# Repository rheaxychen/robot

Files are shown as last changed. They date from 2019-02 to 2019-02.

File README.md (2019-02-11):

# Stair Climbing Robot

*Team 9 - ENGR 202 - Winter 2018 - University of Washington*

Final deliverable can be viewed here: [project deliverable](./stair-climbing-robot-deliverable.pdf), [presentation poster](./Poster/poster.pdf). 

### Reference for file names

*CAPITAL CHARACTER*

- 0 - Cover Profiles Contracts
- A - Project Selection
- B - Project Proposal
- C - Design Concept
- D - Preliminary Design

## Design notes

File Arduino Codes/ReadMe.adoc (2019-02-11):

:Author: aaronsu
:Email: aaronsu@uw.edu
:Date: 02/02/2018
:Revision: version#
:License: Public Domain

= Project: {Project}

Describe your project

== Step 1: Installation
Please describe the steps to install this project.

For example:

1. Open this file
2. Edit as you like
3. Release to the World!

== Step 2: Assemble the circuit

Assemble the circuit following the diagram layout.png attached to the sketch

== Step 3: Load the code

Upload the code contained in this sketch on to your board

=== Folder structure

....
 sketch123                => Arduino sketch folder
  ├── sketch123.ino       => main Arduino file
  ├── schematics.png      => (optional) an image of the required schematics
  ├── layout.png          => (optional) an image of the layout
  └── ReadMe.adoc         => this file
....

=== License
This project is released under a {License} License.

=== Contributing
To contribute to this project please contact aaronsu <aaronsu@uw.edu>

=== BOM
Add the bill of the materials you need for this project.

|===
| ID | Part name      | Part number | Quantity
| R1 | 10k Resistor   | 1234-abcd   | 10       
| L1 | Red LED        | 2345-asdf   | 5        
| A1 | Arduino Zero   | ABX00066    | 1        
|===

=== Help
This document is written in the _AsciiDoc_ format, a markup language to describe documents. 
If you need help you can search the http://www.methods.co.nz/asciidoc[AsciiDoc homepage]
or consult the http://powerman.name/doc/asciidoc[AsciiDoc cheatsheet]

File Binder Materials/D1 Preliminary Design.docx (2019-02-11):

Aaron Su

Caelen Coe

Noah Whelan

Mahamed Dirie

Rhea Chen

Valentina Valero

# Preliminary Design

### Electrical System Schematic

<Insert at end of lab>

Technical Drawing

No major changes have been made since the previous Technical Drawing Section. Please refer to Concept Design section “Preliminary Technical Drawings” and figures 5-10 for all technical drawings.

### Digital Models

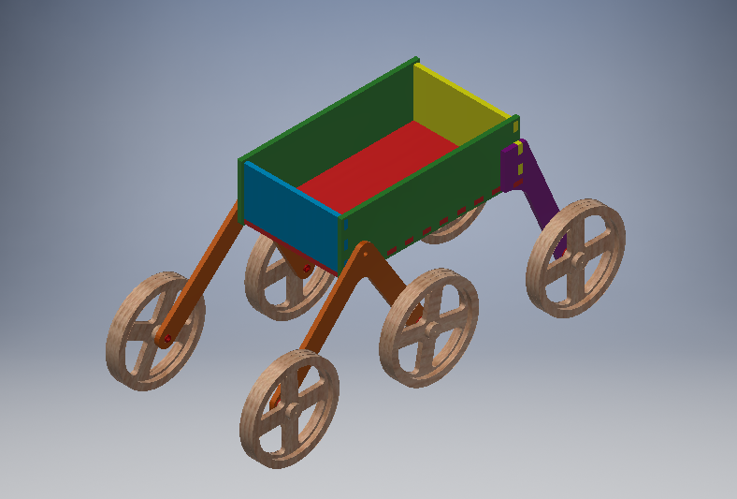
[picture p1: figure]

Figure 2: Design 1, Isometric View of Parts

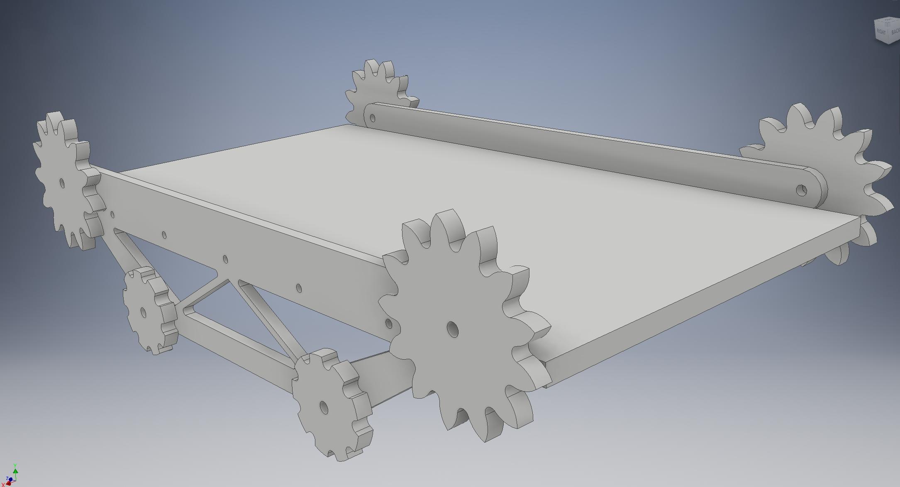
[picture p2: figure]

Figure 2: Design 2, Isometric View of Parts

Both designs are assembled and can be seen in Figure 1 for Design 1 and Figure 2 for Design 2. Design 1 and Design 2 will both take advantage of laser cutting when possible in order to save time and PLA material. This means the panels of the chassis, wheels (Design 1), supports for drive train (Design 1 and 2) and sprockets (Design 2) will all be laser cut. Smaller pieces, such as the axles in Design 1 and individual tracks on Design 2 will be 3D printed in order to be accurate and be made out of non-wood material.

Both designs use a simple chassis that is a rectangular box in order to conveniently have access to the electronic systems of the robot. In addition, the rectangular box is hollow in order to reduce weight, and leave room for the 1.5 kilogram weight that will be carried on board. The drive train will attach to the chassis in order to ensure the robot can be held together.

Design 1 takes advantage of wheels in order for the weight to be light and the frame to be rotatable in order to climb stairs. The front wheels are attached in order to maximize surface area contact with the stairs. Each wheel is also independently powered in order to allow “full-wheel drive” and generate torque when the wheels are in contact with any surface. The back wheel does not rotate since having all sets of wheels rotatable will make the robot unstable when climbing over multiple stairs. The back wheel is meant as an extra surface to ensure the robot will not fall backwards. This design will require an additional H-bridge, axles, and two motors in comparison to Design 2.

The files for Design one are specifically as follows:

Axel and Wheels

- Axel.ipt
- Front Wheel Base.ipt
- Rear Wheel Base.ipt
- Wheel Inner Ring.ipt
- Wheel Inner Spacer.ipt
- Wheel Main.ipt
- Wheel Outer Right.ipt

Vehicle Panels

- Vehicle Bottom Panel.ipt
- Vehicle Front Panel.ipt
- Vehicle Rear Panel.ipt
- Vehicle Side Panel.ipt

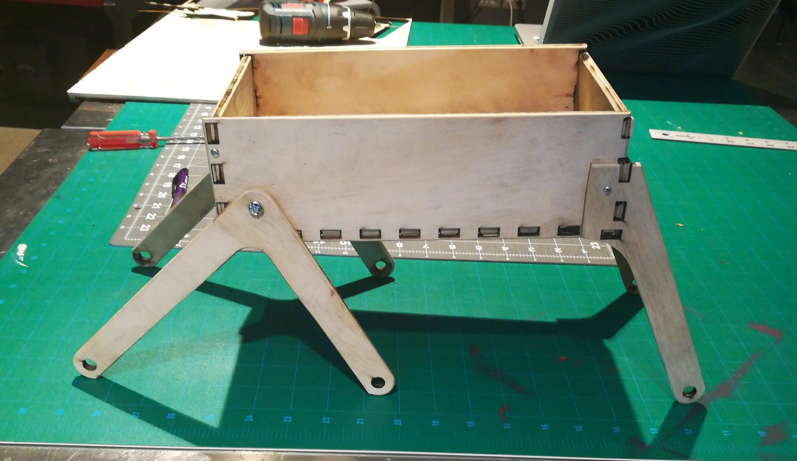
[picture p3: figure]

Figure 3: Design 1, Prototype Side View

In addition, a prototype cutout was made for Design 1 (Figure 3). This was cut out of birch wood to show that the design was technically feasible.

Design 2 is still in development, but Figure 2 shows a mostly completed CAD assembly. Design 2 mainly differs from Design 1 in that it will require more than 6 feet of track as opposed to 6 wheels. The track will be powered by 4 motors (2 on each side) in order to supply enough torque. The traction problem is also solved by having a continuous surface in contact with the stairs, albeit in a less flexible shape than Design 1. The gear design will also provide greater torque to the robot’s drivetrain since the speed will be reduced. Design 2 will require fewer electronics components (as stated above) but will require more material and potentially stronger motors in order to work.

### Simple Machines

Design 1 features a lever for the front 4 wheels and a wheel and axle for each of its 6 wheels. The second class lever will get its force from when the wheels apply a force to the stairs and the stairs push back. This will cause the level to rotate around the fulcrum, which is on the robot chassis, and allow the wheels to climb up the stairs and bring the robot with it. This is a simple machine since the force from the stairs pushing back moves the robot, causing work to be done. The wheel and axle machines found on each of the 6 wheels allow a motor to spin each wheel and axle at the same rate in order to cause the robot to drive. The wheel and axle are simple machines on this robot since they apply a force (from the motors) to move the robot and spin themselves. In combination with the lever on the front wheels, the robot will be able to climb stairs since the wheels can move the whole robot and the level will allow the robot to rotate in order to climb stairs.

Design 2 features gears that are used to power the tracks. The tracks will lay into the gears (of two different ratios) in order to supply maximum torque when the robot is climbing up the stairs. Torque is important in order to overcome gravity and climb up the stairs, meaning the gears are designed to be slow but powerful. It is a simple machine because it helps the robot apply a force coming from the motors against the ground in order to do work to get up the stairs.

The main reason there are two designs is so that we can test the functionality of these two simple machines. Design 1 uses more machines in order to increase the surface area and power applied to the surface through its lever and wheels. Design 2 uses gears to provide torque to the track, but has a smaller surface area by being unable to rotate. As both designs are tested, there will be much emphasis placed on how the design of the simple machines will affect the robot performance.

### Updated Bill of Materials

No major changes have been made since the previous Updated Bill of Materials Section. Please refer to Concept Design section “Updated Bill of Materials” and “Table 1: Updated Bill of Materials Table”.

ENGR202 – Winter 2018 Team 9

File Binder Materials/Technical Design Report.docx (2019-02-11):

Technical Design Report

The Technical Design Report is your chance to show off your project. Explain what you have done this quarter and why it’s impressive. A working project is more important than a well written report, keep your writing brief and to the point.

Your Technical Design Report should at least include the following:

  Explain the changes your design has gone through since the Preliminary Project
  Design and why you made those changes:

Since the preliminary project design the stair climbing robot has changed significantly. The design that incorporated two independent pairs of rhomboid tank treads was reconsidered due to time and material restraints. Ultimately, the group decided that this design would most likely be too costly and complicated. From there the mechanical team split into two different groups. One of these groups designed a robot that utilized a single pair of large trapezoidal tank treads, with two motors powering each tread. The second team designed a robot that utilized six independently powered and controlled wheels attached to stilts that separate them from the chassis. Two pairs of wheels would be connected together at the front of the robot and would be attached to the chassis via an axle that allowed the wheels to rotate around the surface of the stairs. The rear pair of wheels were rigidly attached to the chassis. When each design had been completed we analyzed them as a team to determine which to pursue. Though it was difficult to tell which would perform better at climbing stairs, our team decided that the production of treads for the tank design would be prohibitively time consuming compared to the wheeled design. In addition, the tracked design would require more power and more weight than the wheeled design, ultimately deciding the wheeled design would lead to a better outcome.

Having agreed upon the wheeled design it was prototyped and tested it. During the design iterations several important changes were made. Our first prototype did not have sufficient power to climb the stairs. To remedy this we first replaced our initial small 9 volt DC motors with similar but much more powerful ones. These new motors were 12 volts and ran at 30 RPM or 100 RPM. Secondly, the second prototype chassis was constructed out of acrylic, as opposed to the wood in the first design. This was done to save weight and reduce the amount of torque needed to pull the robot up the stairs. In our third design iteration we added braces to the two forward axles to reduce flexing that caused the wheels to lock up. In addition, after several of our axles snapped we designed new stronger axles that were able to withstand the stress of going up stairs. Springs were also attached to the front-most section of the robot to pull up the robot after the front wheels ran into a flight of stairs. These major changes are what have allowed the robot to improve from being unable to even move up a slight ramp to reliably climbing stairs.

  Include new models and technical drawings

Sections of Chassis (Caelen’s files)

New Acryllic cutouts

  Describe the process you went through in building your projects
  Include process pictures if you have them
  Pictures of completed project

Briefly (1 - 2 paragraphs) describe some of the challenges you faced in the design and building process, and how you overcame these challenges.

Some of the primary challenges we faced during the creation of the robot arose due to monetary and time constraints. In the process of designing our robot we considered multiple designs that incorporated a continuous track or tread. The most time efficient way of creating such a robot would have been to purchase a manufactured tread or belt, 3D printed tracks would have taken too long to print and assemble. Unfortunately we could find no belts of appropriate specifications that would left room in our budget for other important components. Had we the time to print all the necessary track or the money to purchase tread we could have more seriously considered using a tracked robot. Other obstacles also increased the challenge that time posed. One example of this was our reliance on the Dabble Lab. Several times throughout our build process equipment failure meant we would lose a day of work time. Conflicting schedules meant we could often only meet a couple times in a week, meaning a delay of just a day could put us more than half a week behind.

Overcoming these challenges meant adapting our design methods and time management. During our initial design phase we had to take a close look at the feasibility of each proposed design. While the tracked design certainly had its benefits over some of the others, ultimately we determined it to be an unrealistic design path. For all it’s pros it was simply to time consuming to pursue. To save resources and time we stopped our prototyping of tracked designs and put all our effort into producing a functioning prototype that used wheels. Doing this allowed us to fast track our primary design while minimizing waste on designs we couldn’t reasonable build. Time management was also vital in keeping our team on track to complete the robot within the set time constraints. We began to anticipate the possibility of equipment failure. When we planned work sessions we would often set a backup time in the event we couldn’t use the required equipment for progress. We also extended the length of our work sessions to make up for time we had lost previously and to negate the effect of future delays. By proactively responding to these obstacles we have been able to complete our robot on time and within budget.

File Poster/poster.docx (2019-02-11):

It must include what is your project and goal(s). What was the design process? use things such as sketches, CAD, pics of the design, schematics and diagrams to show this. What were the results of your project? Conclusion: whether you met your goals, challenges, next steps if your were to continue.

*** Make a folder/powerpoint all all our pictures used in the presentation so that we have them to present as well***aar

Project

Build a robot that can climb a set of stairs

Robot should be autonomous and hold its own power source

Robot should be able to handle stairs of different sizes

Goals

1. Drive on a level surface
2. Drive on a ramp
3. Drive up and down a set of stairs
4. Operate the Robot with Bluetooth

Design Process:

Concept Design - Narrowed down to two

- Pictures: Sketches of both designs

CAD Designs - Initial concepts of both

- Pictures: CAD of both

Build Designs - Caelan and Noah working in lab

- Pictures: Noah/Caelan Working

Build Electronics - Schematics

- Pictures: Valentina’s electrical schematic

Program - Pseudocode then actual

- Pictures: code (at bottom)

Assemble - Put it all together

- Pictures: Wood design

Test

- Pictures: Us testing

Model 2 - Acryllic

- Pictures: of acryllic bot

Test

- Pictures: More test pictures

Final Design

Conclusion

What we achieved

Robot was fully built and functional

All goals stated above

Challenges:

Choosing the right design

Making the robot powerful enough while minimizing the overall weight

Getting enough power to run the whole style

Building alternate set of stairs when our original design wasn’t working

Next Steps:

Make all motors 12 Volt, 100 rpm motors

Switch out batteries to 12 Volts (currently 18 Volts) to avoid damaging Hbridges

Switch wheel material to rubber to get more traction

Add sensors and accelerometers to get more feedback from robot

Get to point it can climb human-sized stairs

Put on poster:

Stronger Motors

Add Sensors

18V -> 12V Batteries

Pictures

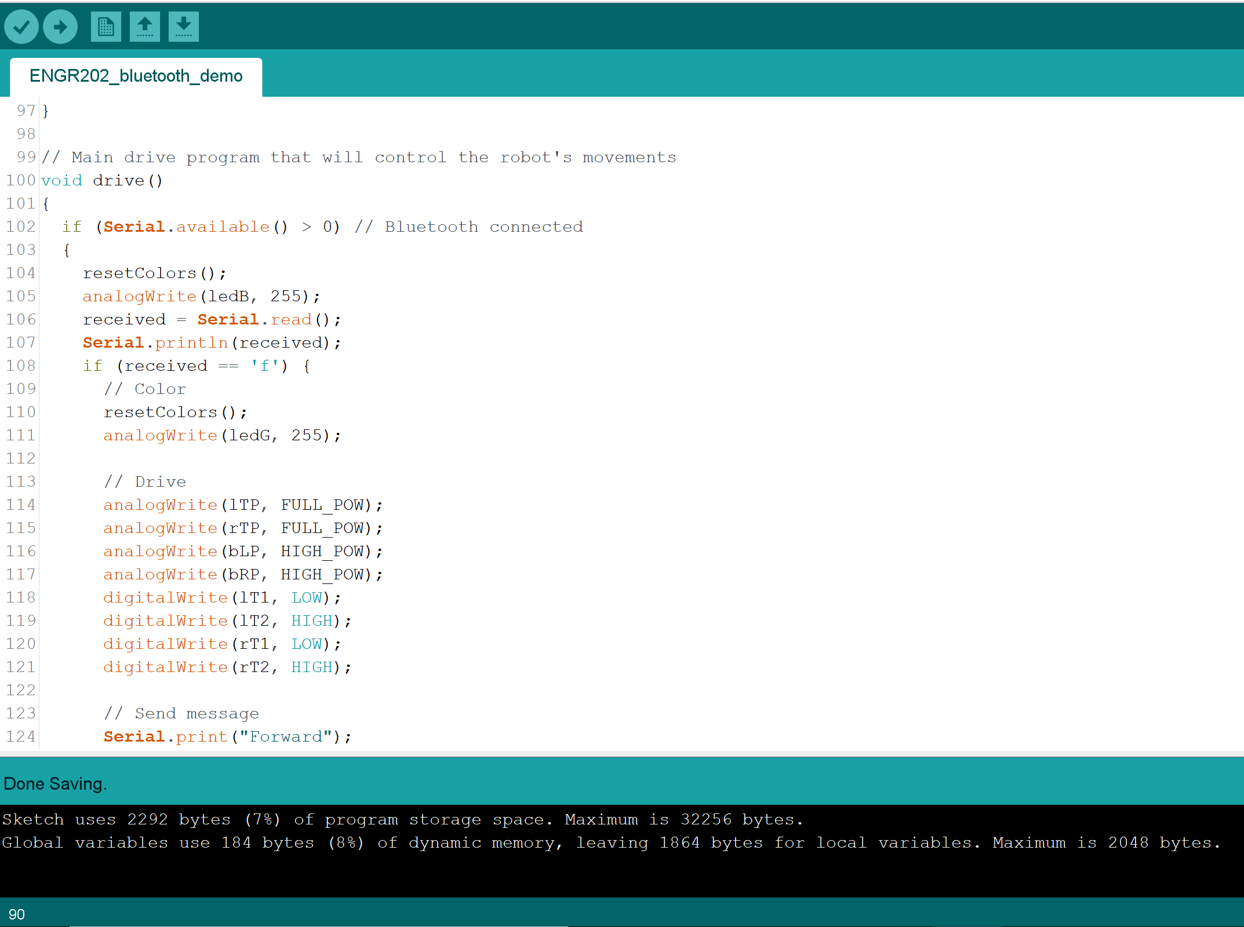
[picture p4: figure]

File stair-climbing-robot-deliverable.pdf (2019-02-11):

1 | P a g e

2 | P a g e

## Table of contents

I. Profiles | 3-6
II. | Team Contract | 7
III. | Project Selection | 8-
| 12
IV. | Project Proposal | 13-21
V. Concept Design | 22-33
VI. | Preliminary Project Design | 34-39
VII. | Technical Design Report | 40-58

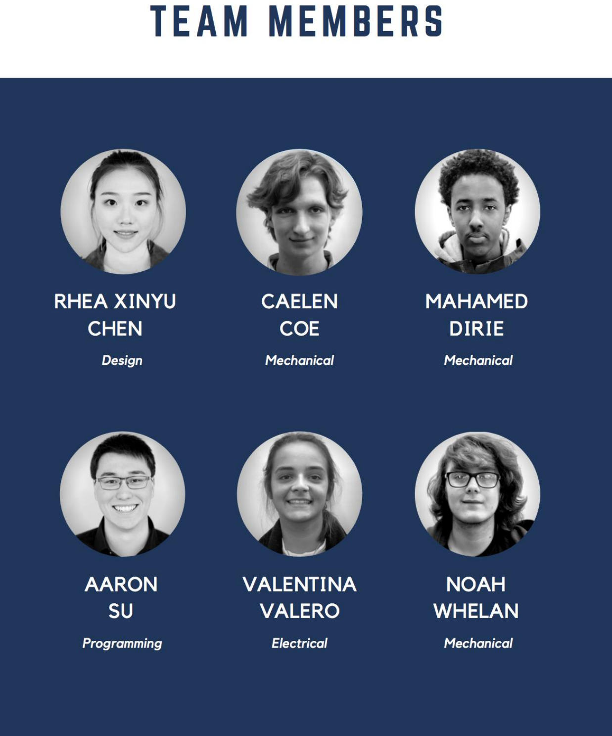
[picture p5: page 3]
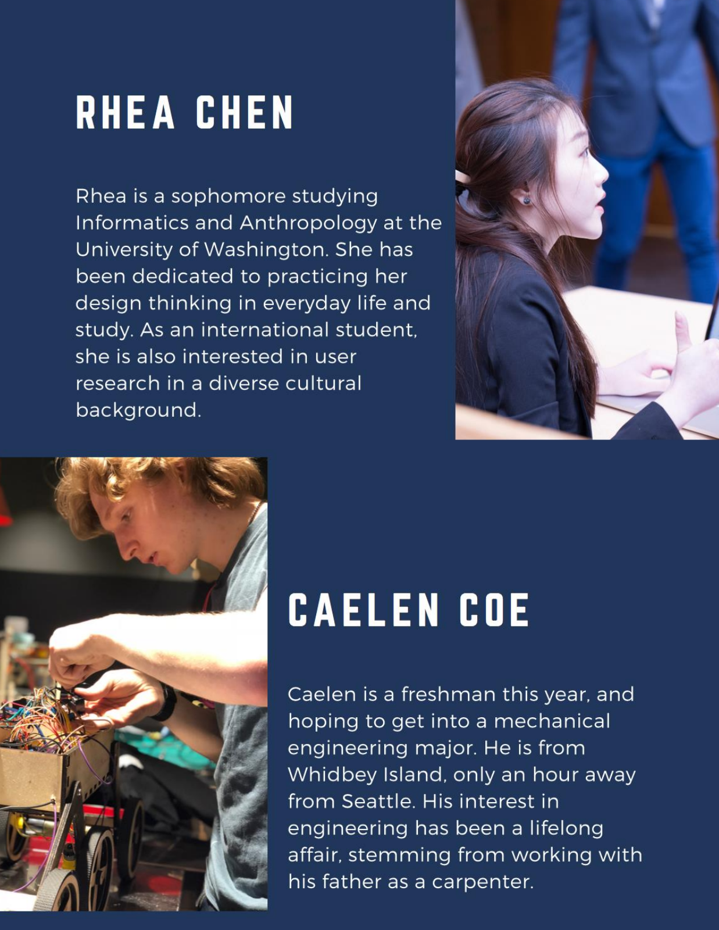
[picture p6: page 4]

4 | P a g e

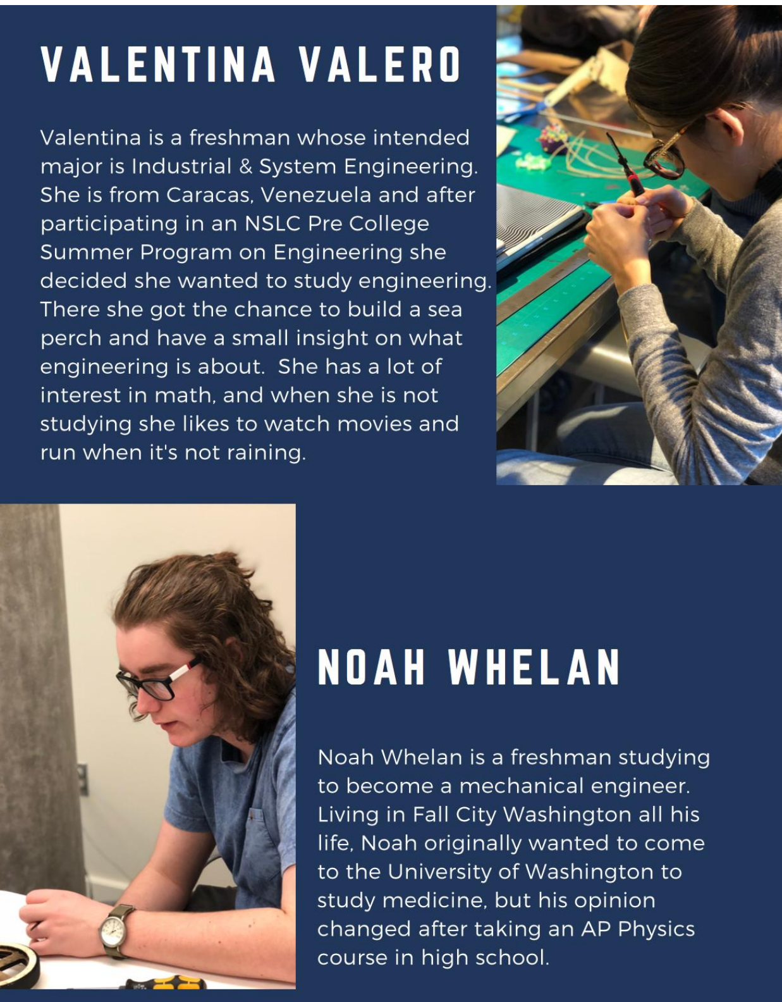
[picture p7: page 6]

6 | P a g e

## Team Contract

## All team members shall do as follow to ensure the best and most successful work environment:

## - Be on time - If you are late, communicate - Be patient - Teach each other - Be responsible - Be honest - Be encouraging - Communicate on Slack - Do not be stubborn when stubbornness is not required - Ask questions if you have any - Solve problems as they arise

8 | P a g e

## Project Selection

Introduction

The members of our team individually brainstormed ideas that the whole team could potentially work on during the quarter. After researching different robots and ideas, each project idea was given a paragraph description under “Project Ideas”. Then, an overall group rating for each project was made in a “Decision Matrix”, allowing the group to narrow down the choices from five to three. These final three selections will be among those considered for the final project, which was selected in the very final section.

Project Ideas

1. Gardening Robot

This project would involve a robot that is able of managing the gardening of a plant. The steps in the planting process which the robot will be capable of are driving in soil, digging up soil, dropping a seed, watering the seed, and fertilizing the seed. This robot has real-world applications that involve simplifying the gardening and farming process that could be used on a personal or industrial level. The parts required for the robot would involve containers and release systems for the seeds, water, and fertilizer that would involve valves and switches. The digging process would involve a motor attached to a drill-like object. FarmBot Genesis is a similar robot on the market that can plant a seed with a seed injector and water it precisely, build regimens for taking care of a plant by using its sensors to detect outside conditions, detect weeds and destroy them too (FarmBot.io, 2016)

2. Object rejection and counting machine (ORCM)

This project would be a robot whose purpose is to reject items that do not fulfill a specific condition, related to size and weight. This would be similar to the “conveyor belt sorting bot” created by Gurmeet Sharma that is able to sort objects based off height (Sharma, 2009). In this example, the object rejection and counting machine has a conveyor belt and a sensor that identifies the size of the object, if the object doesn’t fulfill the condition, it is pushed out of the conveyor belt. It is very useful for quality control and inventory in factories as it can sort out anything that does not satisfy a condition. For example, it can determine whether a tennis ball fulfills certain criteria for size and weight for them to correctly perform. It can also be applied to determine the type of coin based on the weight and size. This project will likely require buying parts because it has a conveyor belt system that uses two or more pulleys; and a load sensor to determine the weight. From the provided parts this project will require a DC motor.

3. Companion Bot

This project would involve an autonomous robot that follows a device through Bluetooth or wireless communication. The robot would be similar to companion bots like Kuri, meant to follow a person around while providing auxiliary services (NBC News, 2017). Kuri is a companion bot that fulfills a wide range of functions that include recognition of faces, playing music or working as an alarm. The robot can respond to the touch and can moves around through any surface thanks to a set of sturdy wheels. Rather than providing all the same functionality as Kuri, the robot would only follow a person around and hold materials that person finds useful (water bottle, phone, speaker, etc.) These personal items will be able to add supportive services to the robot, such as playing music. This project would be useful as a prototype to see how people will want to interact with an autonomous companion bot. The project will focus on avoiding obstacles using distance sensors, following an object through Bluetooth communication, and 3-D printing a customized robot frame to fit the personal items. This project will require a Bluetooth-capable device to communicate with the robot, but a phone with such capabilities is owned by all members of the group.

10 | P a g e
4. Stair Climbing Vehicle

Semi tracked vehicle with ability to climb stairs. Basic design would consist of four independently driven tracked wheels, and an adjustable wheelbase. Would need to have ability for object and environment detection and obstacle avoidance. Required parts would be infrared or some sort of LIDAR for object detection, on-board cameras for driver visuals, multiple motors and servos for movement. An example of the final robot would be like the robot designed by Transcend, which is built to assist police by climbing upstairs using a tread drive base (Transcend Tactical, 2018). Thought the example is much more complex than what is being planned, the robot can ascend 3 steps at a time in up and down articulated movements that produce a downward compression force.

5. Kitchen Aid Robot

This project would be an autonomous robot that could crack an egg by following set movements, or a robot that could make a cookie dough given the specific amount of each ingredients. This robot will only focus on one single task following a pre-programmed set of movements similar to Molly’s Kitchen Robot prototype (UPHIGH, 2016). This bot will be able to use a motor to spin, raise, and lower the arm, and use precise movements to ensure nothing gets broken in the process. The robotic kitchen has a pair of fully articulated hands that reproduce human movements when cooking and is operated through a touch screen. This project will save people time and effort in cooking. To prevent it from crashing due to water, we would add water-proof layer to it.

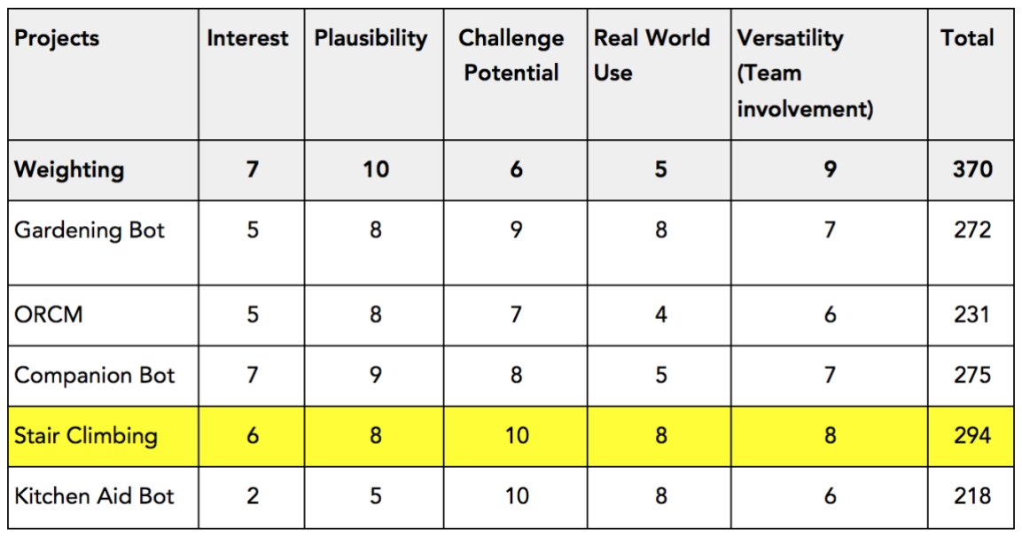
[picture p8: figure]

Decision Matrix

Table 1 - Decision Matrix

In our Decision Matrix (Table1), interest (Col.2) was our third most important category in order to keep us motivated throughout the quarter in order to want to spend time on this project. Plausibility (Col.3) was the most important category to our group since we all wanted a finished product at the end of the quarter with the parts provided. Similarly, versatility (Col.6) was our second most important category since we wanted to keep all interested team members involved in a project they could finish. Challenge potential (Col.4) was also considered so that if a particular part of the project was done quickly, there was the ability to increase the scope of the project. Also, challenge helps us think out of the box to help us solve problems that may come up. Finally, real-world usage (Col.5) was considered since our project is a prototype to solve a real-world issue.

12 | P a g e

1st Choice - Stair Climbing

The team thinks this project would provide a challenge in design and execution, and is thus our top choice. We also believe that the driving mechanics associated with independently powered wheels would be sufficient work for the mechanical, electronic, and programming sub-teams. There is potential in this project to be able to handle different stair sizes ranging from smaller than the robot’s wheels to human-designed stairs, meaning we can adapt this project to our engineering ability.

2nd Choice - Companion Bot

This project allows for a creative component and allowance for differing levels of complexity. The idea of making a robot for personal use is one that appealed to many members of the group, as it would serve our own purposes after it is complete. Also, the challenge of getting a robot to drive and follow a device should give the programming and electronics sub-team plenty to work on.

3rd Choice - Gardening Robot
This project is the most multifaceted of the three final projects since it will do more than just drive. The different subsystems required to fully garden a plant provide plenty of opportunities to design creatively and allow the project to adapt to our own skill sets. The practicality of the bot combined with the team involvement and ability to finish it make this one of our top three choices.

Final Decision

As our final decision, we decided to work on the stair climbing robot due to its challenge potential for both the mechanical and electrical sub-teams. There are many possibilities in the design of the robot as well, which gives our team opportunity to brainstorm.

## Project Proposal

Introduction

Robots are increasingly being integrated into working tasks to replace in many fields of applications such as military, security systems, agriculture and industry. The project’s goal is to prototype a specific implementation of a stair-climbing robot in order to contribute to the body of knowledge and work done in this field of robotics. The robot’s functionality will focus on being able to climb up a set of stairs as well as move over a flat surface, and rather than building the robot with expensive materials or the most advanced machinery, the project will focus on applying fundamental engineering principles and a relatively small budget to design, prototype, and build the robot. This will allow the project to be accessible and by any individual or group that has a basic understanding of engineering design, such as students in an undergraduate introductory engineering course.

Problem Statement

For military/police investigation, surveillance, urban search and rescue missions is often necessary to place sensors and cameras to get better awareness for the rescue personnel on the situation in order to determine how to proceed, for this reason stair climbing robots are a great alternative to reach dangerous or inaccessible areas just by the use of a control remote. Robots have a clear advantage over humans in these situations and the benefits to this operation of rescue robots, such as a stair climbing robot, include reduced personnel requirements, reduced fatigue, and access to unreachable areas. Robots are predestined to complete this task, but the requirements for such mobile systems are demanding. They should be quick and agile and, at the same time, be able to deal with rough terrain and even to climb stairs. By finding effective ways for robots to climb stairs, the safety of professions including firefighting, relief workers, soldiers, police officers, security guards, and professional movers will increase.

14 | P a g e

Objectives

1. Moving on a Flat Surface

The robot should be able to move on a level ground at a constant speed of 0.894 mps. We decided the speed taking as a reference the walking speed. Constant speed is important for comfortable driving over surfaces that aren’t stairs, which many stair-climbing robots might also be forced to do.

2. Moving up an inclined surface
The robot should be able to drive up a smooth inclined surface, specifically a wheelchair accessible ramp. The angle of the inclined surface is approximately 4.76°, which is the required angle by the Americans with Disabilities Act. Our robot needs to successfully climb a ramp in order to achieve the simple task of climbing up an incline that a normal wheelchair would be able to do, which has a length of approximately 4 feet. This value is also determined by the Americans with Disabilities Act.

The robot should be able to climb one single step of stairs and stop on that stair, its body being completely on the stair. This is important to test the capability of our robot when climbing over smaller obstacles, such as a small hill or sidewalk. If the robot cannot climb a single stair, there is no possibility the robot can climb the rest of the stairs.

The robot should be able to climb an entire flight of stairs without stopping. This is the main goal of the project, as being able to climb a set of stairs without being stopped by any technical problem since it is most likely that in the use of urban areas the robot will be required to move from one location to another. The chosen set of stairs to climb fully is the main stairs of Area 01 in Maple Hall on the campus of University of Washington.

The robot can climb an entire flight of stairs with the ability to stop part way through before continuing to climb. This is important to ensure that if a robot stalls on a staircase that it is able to recover and continue executing its mission. The chosen set of stairs to climb, stop, and continue climbing is the main stairs of Area 01 in Maple Hall on the campus of University of Washington.
3. Climbing a set of Stairs with Each Individual Step at a Fixed Type

Even though there are many types of stairs, the prototype will focus on climbing a specific set of stairs, which are a combination of boxes stacked on top of each other. The height of the stairs is 3.5’’. This height was determined by the height that was

70% the diameter of the wheels, a reasonable task for a robot. We decided this type of was acceptable given the budget and power constraints of the robot. The robot will successfully accomplish this goal if it can climb up and down the flight of stairs without stopping.

4. Driving the Robot through Bluetooth

The robot should be able to connect to a Bluetooth-enabled device that will give it instructions to move up a flight and stairs and move down. Remote control is essential to make sure the robot can perform in environments that humans cannot easily access. The robot will have accomplished this goal if it can move, brake, change direction, and do all tasks stated previously while receiving directions from a Bluetooth device.

5. Carry a payload of 1.5 kg
Being able to carry additional equipment beyond its own weight adds a large amount of versatility to the possible uses of the robot. This could include:
- Carrying a camera to allow the pilot to operate it without a line of sight.
- Deliver small parcels, such as supplies to someone who is trapped inside a building.
- Allow for the use of more robust and heavy parts if necessary.

We chose 1.5 kilograms as this is heavier than the weight of many common objects, as well as 1.5 liters of water, most types of batteries, and standard medical kits. The robot will successfully accomplish this goal if it can do all tasks stated previously on the chosen set of stairs.

16 | P a g e

Background Research

Stair climbing robots aren’t something this project needs to invent. There are numerous working designs for such robots that have been implemented for different uses (Robotpark ACADEMY, 2013). This project will not just copy one of these designs because, besides simply wanting to design something new and unique, there are different restraints and goals. For example, limits in time, money, and resources restrict certain designs, such as those with articulating legs (Lucidarme 2008). Also, the simpler designs, such as DeeDeLogists arch bot ("Stair Climbing Robot by DeeDeLogist" 2011), should not be used since the team has agreed on a certain level of challenge to meet. While another design will not be copied, common elements of functional stair climbing robots can be incorporated to the design of a new robot around this project’s constraints.

Many of the important features of stair climbing robots are based on where the robot comes in contact with the stairs. The main goal in this area is to enable the robot to push itself up the stairs without its contact points slipping down. The simplest way this is done is by using a material with a high coefficient of friction, like rubber (Townsend 2002), as the contact surface. Most robots also use a dynamic base that in some manner changes to better conform to the stairs and maintain constant contact as the robot goes up. This can be done by using flexible treads that bend to the surface of the stairs ("Stair
Climbing Robots And High-Grip Crawlers | Intech" 2010), robots with multiple pivoting
wheels (Watt 2011, Mohan 2014), pivoting treads (Lucidarme 2008, "Stair Climbing
Mobile Robot - ARTI: Rugged Commercial Platform | Transcend Robotics" 2016, "Stair
Climbing Robot" 2011), or even static “wheels” that are designed in such a way to change their effective radius as they rotate to match the shape of the stairs ("Stair Climbing Robot" n.d., "Stair Climbing Robot (Triple Bended Crosswheels)" 2013, Yap 2017). Designing with this in mind will ensure that this robot will maximize the amount of static friction, as opposed to the weaker kinetic friction (Townsend 2002), enabling the robot to push itself up the stairs instead of stationarity spinning its wheels.

Another important aspect of a stair climbing robot is managing its center of gravity and base of support (Gupta 2015). Even if the robot can stop from sliding down the stairs, there is still the possibility of it tipping over. In bipedal walking/climbing systems, a system’s center of gravity will go outside the base of support, because in essence bipedal walking is repeatedly falling and catching oneself ("Base of Support" 2017). This project will have a bipedal climbing system for this reason it will always have to keep the center of gravity above the base of support. By moving on the ground this is simple, using four wheels as the outermost points on a vehicle will ensure the center of gravity is always above the base of support. On an incline like stairs, however, the base of support becomes smaller and the center of gravity moves backwards. Both the base of support and center of gravity also change as the robot goes over the bumps of the stairs. To overcome these challenges stair climbing robots are generally designed with low centers of gravity, so the change is not as large and with wide bases of support. Most robots are also designed to counteract the oscillating surface of stairs, such as by designing the wheels to minimize change in center of gravity. Designs like that include the crossbend wheel robots ("Stair Climbing Robot (Triple Bended Crosswheels)" 2013, Yap 2017) or independently moving sectioned robots (Lucidarme 2008, "Stair Climbing
Mobile Robot - ARTI: Rugged Commercial Platform | Transcend Robotics" 2016). By
using these principles, the robot will be able to ascend without tipping or rolling down the stairs.

The final research consideration to make is what type of robots will be possible to build with the materials and methods available. With access to 3D printing technology, the manufacturing of parts that would normally increase a budget, like a planetary reduction gear set ("Planetary Gear by Ngoodger" 2014), can be done at a fraction of the cost. While rubber tread may be too expensive to purchase, 3D printing tank tracks ("Continuous Tank Treads by Whowhatwhere" 2010) and assembling them is a cheaper alternative. If a wheeled design is chosen instead, a laser cutter can do most of the work. Prototyping different wheel designs in cardboard can also be done conveniently before cutting the final wheels out of other materials. These tools provide considerable freedom in developing the robot.

Plan of Action

1. Using Tracks

Firstly, tracks provide a larger surface area engaged with the stairs, as opposed to wheels which have an extremely small area touching the surface. Secondly, 3D printable track links are already available online, along with compatible drive wheels. Additionally, tracks allow us to modify the size and shape of the track without having to remodel anything, links can simply be added and removed.
2. Two Tread Pairs

A robot that only used one pair of treads (similar to a tank) would experience a higher degree of center of gravity shift & base of support reduction, causing tipping to be more likely. Three or more pairs of treads would add a large amount of work and would be unlikely to fit within the size constraints. Two pairs affords a flexibility between the chassis and the tracks without making the system too complicated. Additionally, the triangular shape is the strongest one because it is an inherently

18 | P a g e

rigid structure, as the angle between the sides is determined directly by the length of the sides, as opposed to shapes with more than three sides where the angle and length of the sides are independent of one another. The robot will have four individually powered tracks of isosceles triangle (two sides of equal length).
3. Slot for Additional Weight in Middle/Electronics

A specific area designed to hold our mass will help prevent unexpected shifts in the weight that could cause the robot to slide or topple over. Electronics will also be stored in the middle of the robot, including the Arduino, breadboard, and main wiring, battery, and Bluetooth receiver. This is to keep the center of mass as close to the middle of the robot as possible to prevent sideways tipping.
4. Independently Powered and Controlled Treads

In order to successfully achieve our design goal of climbing stairs, we plan to give each tread its own power source to increases the torque/output of each tread. Using controlled treads gives us the advantage of less drivetrain or other power transfer system which decreases the design complexity and reduces number of parts that can fail. The high-flexibility feature of controlled treads increases the robot’s mobility and allows the robot have different treads moving toward different directions and at a various speeds and do regular and zero-point turning.

Bill of Materials

Table 2 – Bill of Materials (original)

20 | P a g e

Development Plan

Table 4.1 – General Development Plan

Table 4.1 lists out all the group project assignments’ due date and gives a clear timeline for the design process. It serves as notice board for reminding each team member of their own duty.

Table 4.2 – Project Management Plan

Table 4.2 is meant to facilitate better team communication for higher productivity.

Table 4.3 - Mechanical & Electrical Development Plan

Table 4.3 relies on our ENGR202 course progress. Our knowledge level in these two domains is the main constraints of our project development plan. It provides a clear development guideline for both teams based on our course schedule and group assignment due dates.

Conclusion

A stair climbing robot has applications in a variety of settings and situations where human lives are at risk of danger for these reason there are many applications of stair climbing robots in the military, disaster aid, and professional moving industries that we hope to build upon and incorporate into a unique design. The project will strive to accomplish all goals related to climbing stairs, including stopping on a flight of stairs as well as carrying a payload, and moving over a flat surface at a constant speed. By focusing on executing fundamental engineering design principles and enhancing designs from previous implementations, the project will be able to successfully create a stair climbing robot.

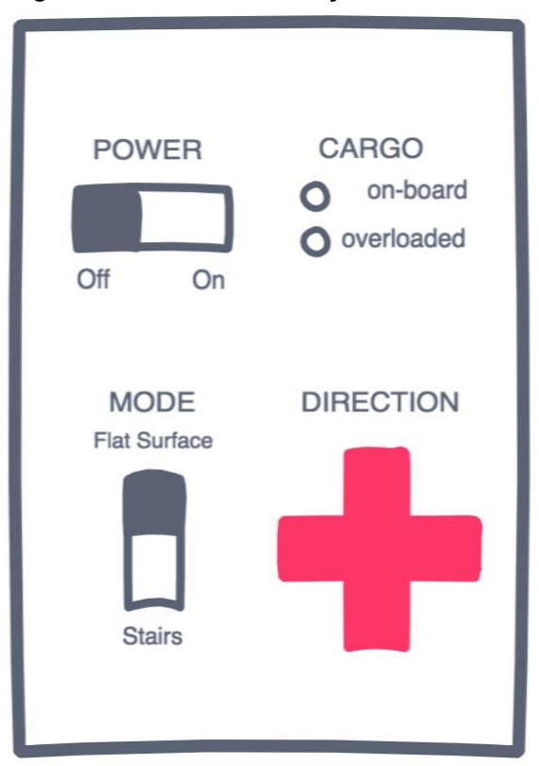
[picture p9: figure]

22 | P a g e

## Concept Design

Design Requirements

The project will be a Bluetooth-driven, stair-climbing robot. The robot will be capable of climbing stairs of which each step is 5 inches tall and 12 inches long through a multi-wheeled design. The robot will also have to pull up a 1.5-kilogram weight, making the design of the robot light and sturdy but also requiring independently driven wheels. Finally, the robot will have to have its own power source and Arduino in order to be controlled over Bluetooth.

User Interface

Figure 1 - Screen Interface 1: Power Off The main users of the project will be staffs or drivers who will control the robot to travel to a desired destination, either with or without cargos. Our users are intended to have similar skill and ability as actual users of a commercial stair-climbing robot, such as security officials, military officers, or professional movers. Considering our users’ diverse cognitive affordances, such as language, and education background, we will implement our user interface on either a tablet or on a remote controller, with buttons labeled with universal symbols and colored in shared convention.

There will be a direct screen interface on the application of the robot as well as a direct non-screen interface on the robot. The “power” switch will be both on the robot and on the application and will function as the regular and emergency stop button to cut power to all robot systems. The “power” switch control will be in passive mode: it requires user input to turn on and turn off the power. The application will provide further interaction with the robot as it provides direction buttons that take inputs from users. The robot will also take a series of implicit inputs as default values including the surface mode (flat, incline, or stairs) and the weight of the robot. The direction switch will be in active modes: if the user doesn’t press any direction, the robot will not move.

Several of the indirect interfaces include lights to indicate if the robot is loaded with cargo and to

indicate if the robot is in “drive” mode. The constraints of the robot include the restriction on movement if the robot is overweight or if the robot is not in drive mode.

24 | P a g e

System Environment

The complexity of stair‐climbing involves more than climbing over an obstacle or going up a slope. For this reason, it is important to take into account the environment in which the system will be operating. The system is expected to operate in a flight of stairs by being able to climb steps one at a time. The location will be Maple Hall in the University of Washington. Each step will have a height of 5⅝ inches, and the stairs will vary in characteristics such as the material and whether or not it is a backed stair. There will also be external entities that may interact with the system such as the weight that the stair climbing robot will be carrying, which will be approximately 1.5 kg.

Since the environment in which the system is expected to operate may vary greatly, this will affect the functionality of the robot. A backless stair means that as the robot moves up the flight of stairs, it can fall through the gap while in the process of moving from one step to another. This means that the robot will have to have a large chassis and large wheels to avoid falling through. Also, the different materials of the stairs may affect the mobility of the robot, with surfaces such as carpeted stairs producing more friction with the wheels. This means the wheel design has to be versatile in order to be slicker on rough surfaces and grip on smooth surfaces.

In terms of external factors to the stairs, people walking up or down the stairs can impede the robot’s movement. In addition, if the robot were to drive outdoors, precipitation or wind can also cause problems for the robot’s stair traversal. Currently the robot is only intended to be driven indoors, but an outdoor modification for the robot would include shielding for the electronics and sensors to detect for people.

System Input/ Output

Figure 1 details how the robot will process different Bluetooth commands it will be given. The commands will be a variety of driving instructions that can cause the robot to go in four different direction; forward, backward, to the left and forward, and to the right and forward. The Arduino on board of the robot will interpret each command and power the motors in the commanded way. The direct processes occurring on the Arduino will be certain motor operations given to each of the independently powered wheels. This will include instructions for the number of rotations each motor needs to make (given in units of seconds) and a direction (a Boolean value for forward if true and backwards for false). In the case of all wheels given a time and positive Boolean, the robot will drive forward. In the same case but a negative Boolean, the robot will drive backward. In the case only the right wheels are told to drive, the robot will turn right. In the case only the left wheels are told to drive, the robot will turn left.

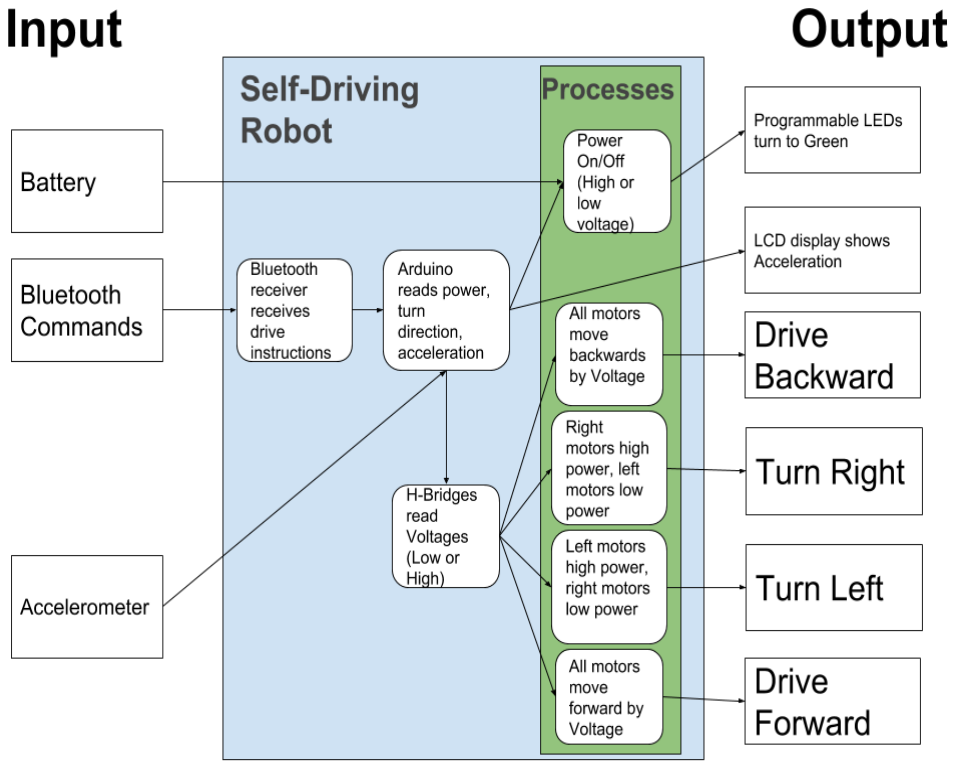
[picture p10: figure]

Figure 2 - I/O Diagram

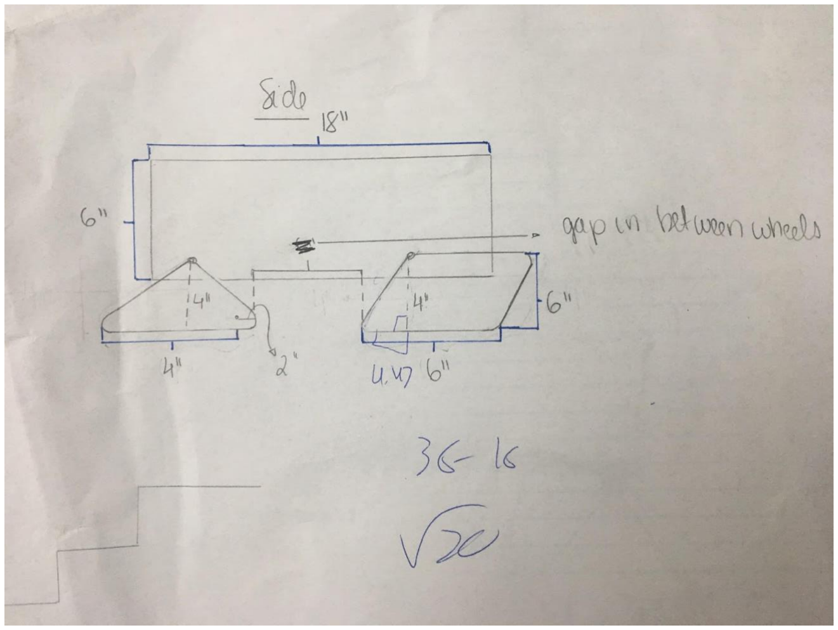
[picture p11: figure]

26 | P a g e

Concept Sketches

Figure 3 - Sketch 1: Concept Design (side view)

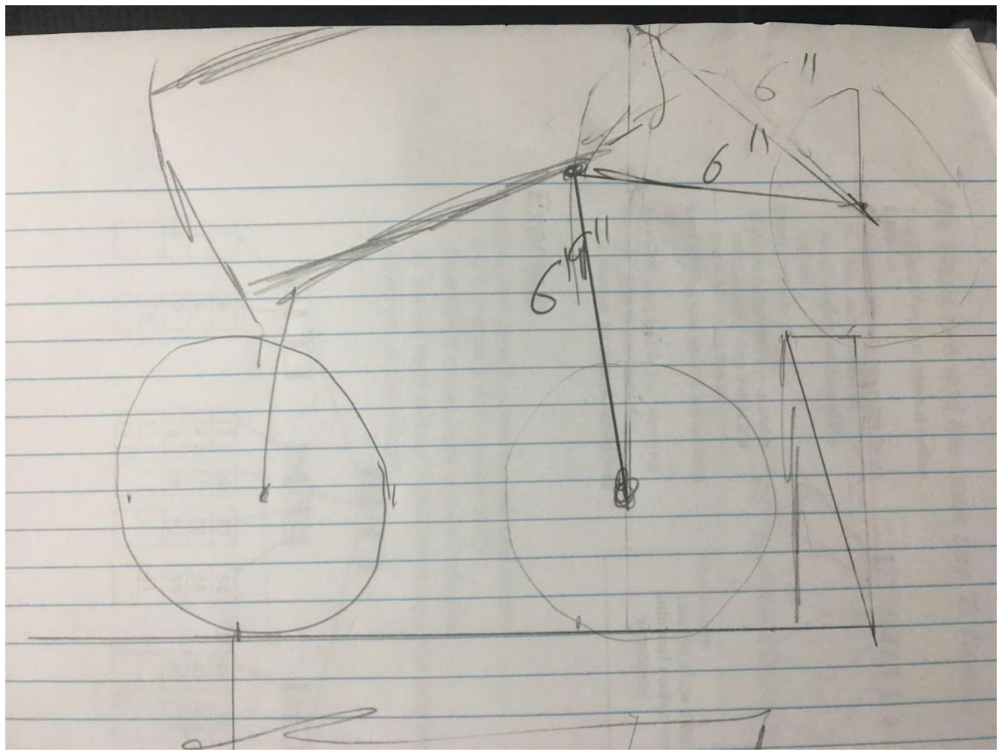
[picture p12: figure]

Figure 4 - Sketch 2: Ideal Climbing (side view)

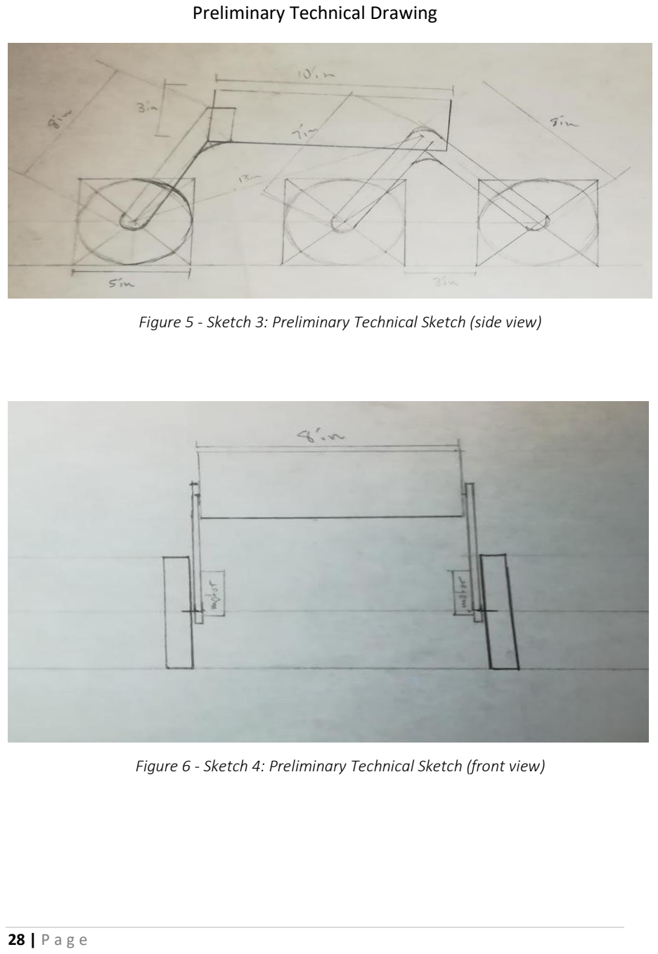
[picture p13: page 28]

28 | P a g e

Preliminary Technical Drawing

Figure 5 - Sketch 3: Preliminary Technical Sketch (side view)

Figure 6 - Sketch 4: Preliminary Technical Sketch (front view)

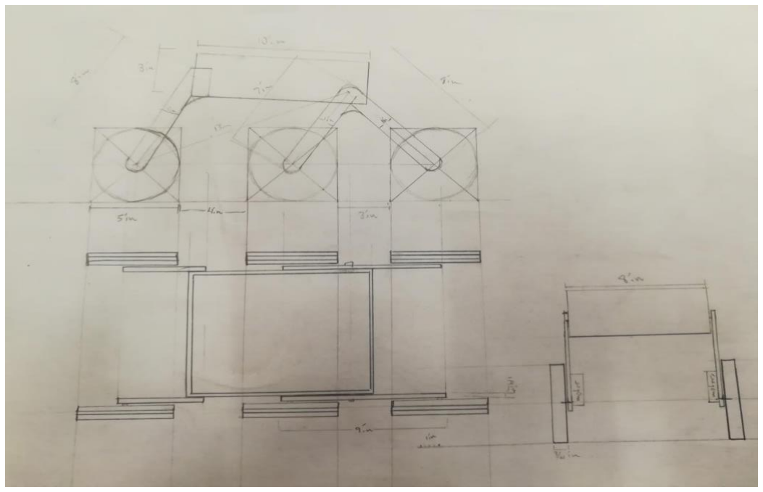
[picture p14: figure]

Figure 7 - Side, front and top view of Preliminary Technical Sketch

The first design (Figure 5 and 6) will have a 6-wheel design with the forward two front wheels attached together to better climb stairs and the back wheel providing stable support (Figure 5). Each wheel will be of the same composition and size. The brackets that attach the chassis to the wheels will also include springs (Figure 5) which will allow controlled movement of the wheels. Each wheel will also have attached motors on the underside of the robot (Figure 6). The chassis is meant to be small and lightweight in order to store the battery, Arduino, Bluetooth module, and additional weight in a safe and enclosed manner.

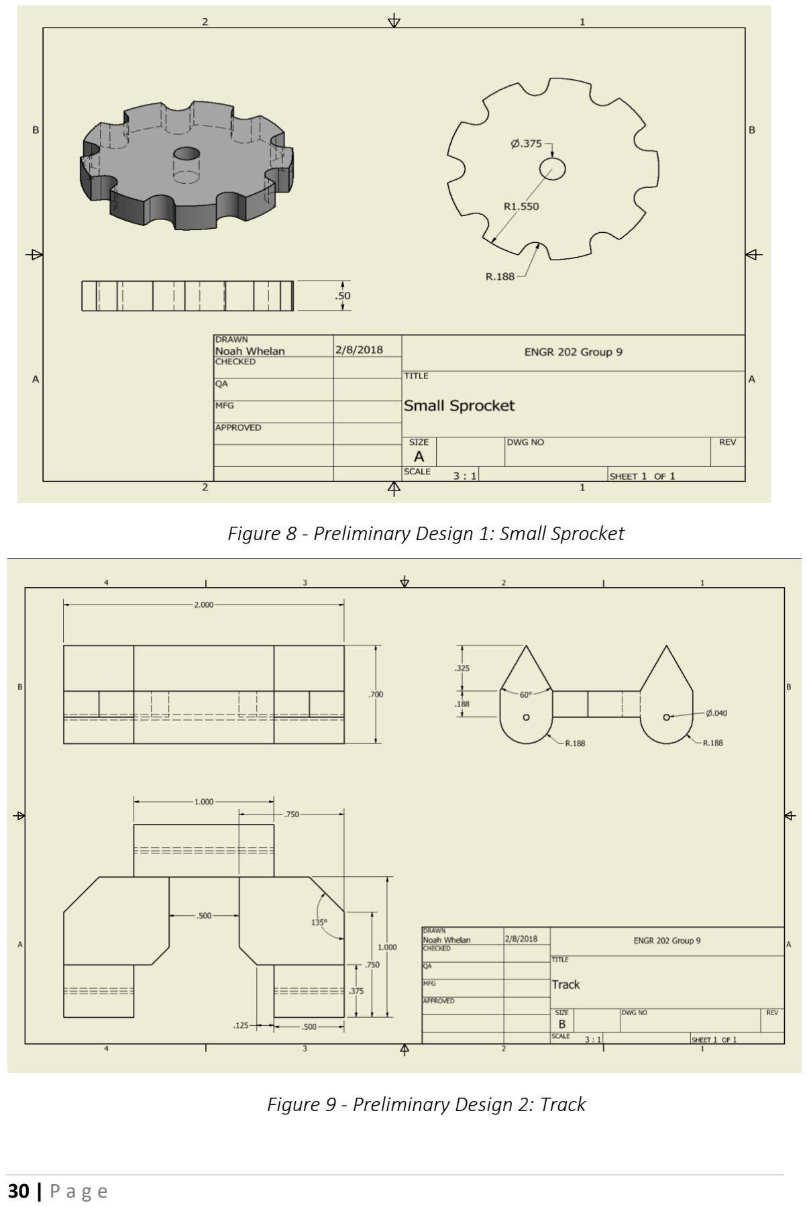
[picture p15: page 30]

30 | P a g e

Figure 8 - Preliminary Design 1: Small Sprocket

Figure 9 - Preliminary Design 2: Track

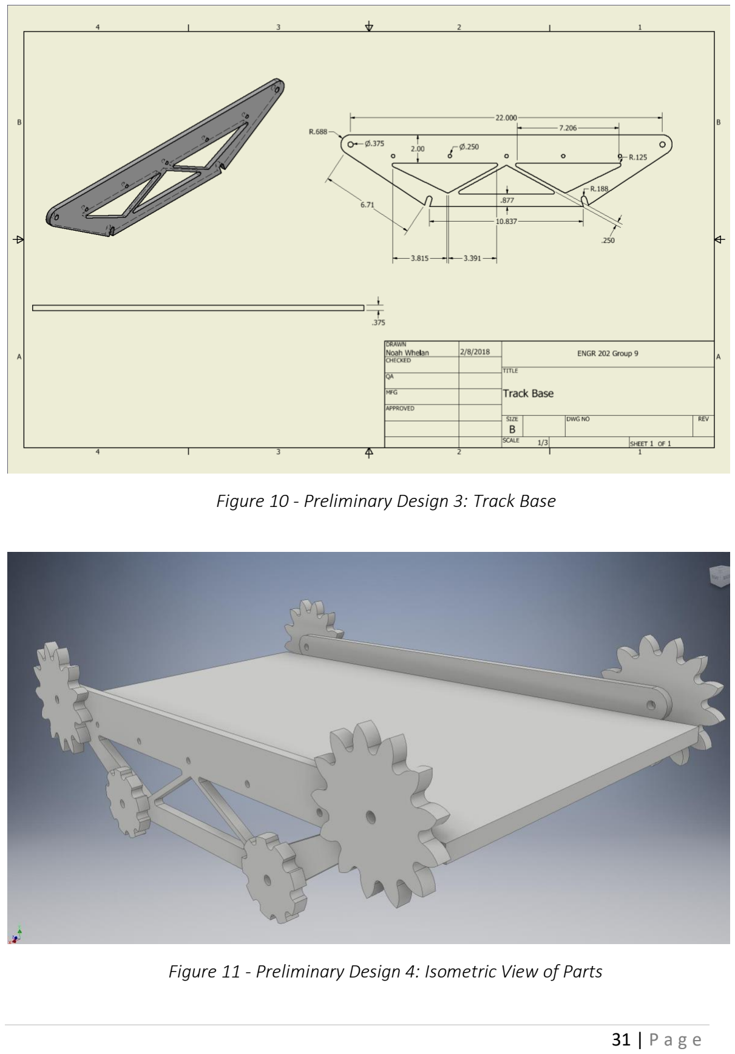
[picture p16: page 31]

Figure 10 - Preliminary Design 3: Track Base

Figure 11 - Preliminary Design 4: Isometric View of Parts

32 | P a g e

The second design (Figures 8-11) shows a full track in place of wheels that will provide the main support to climb over stairs. The tracks (Figures 9-10) will be attached to the chassis and be powered with gears (Figure 8). The final form of the robot of Design 2 (Figure 11) shows that the wheel design, which might fail on stairs without a backing, can be overcome with this particular arrangement of parts. Both designs will be prototyped going forward. The tracks will be powered with 4 motors, one on each corner of the vehicle.

Updated Bill of Materials

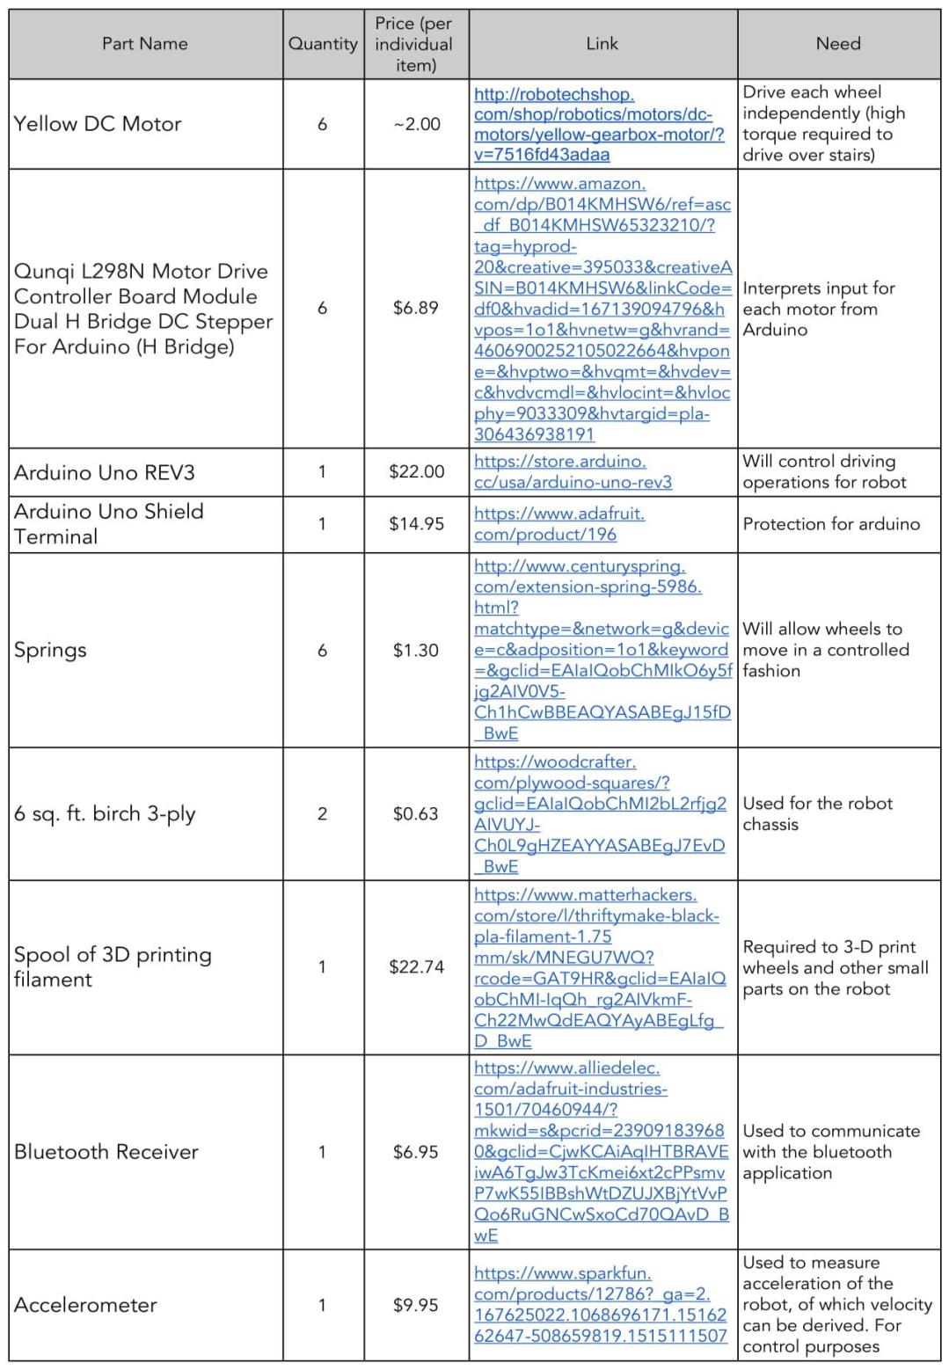
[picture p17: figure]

Table 3 – Bill of Materials (updated)

34 | P a g e

## Preliminary Project Design

Electrical System Schematic

Figure 12 – Breadboard

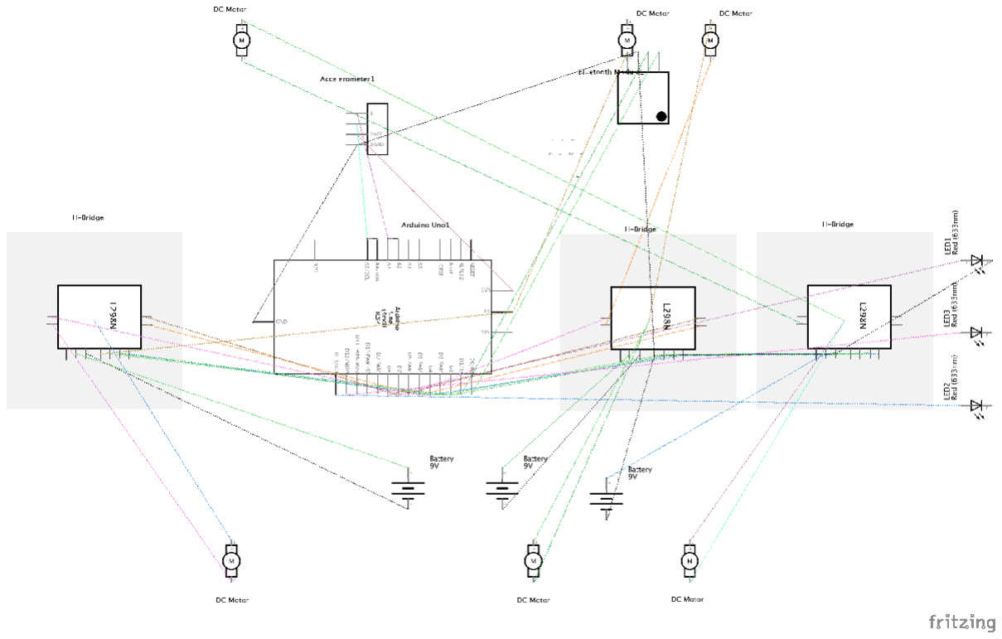
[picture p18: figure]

Figure 13 - Electrical System Schematic

Technical Drawing

No major changes have been made since the previous Technical Drawing Section. Please refer to Concept Design section “Preliminary Technical Drawings” and figures 5-10 for all technical drawings.

Digital Models

36 | P a g e

Figure 14 - Preliminary Design 5: Isometric View of Parts

Both designs are assembled and can be seen in Figure 15 for Design 1 and Figure 11 for Design 2. Design 1 (Figure 15) and Design 2 (Figure 11) will both take advantage of laser cutting when possible in order to save time and PLA material. This means the panels of the chassis, wheels (Figure 8), supports for drive train (Figure 8 - 9) and sprockets (Figure 9) will all be laser cut. Smaller pieces, such as the axles in Design 1 (Figure 15) and individual tracks on Design 2 (Figure 11) will be 3D printed in order to be accurate and be made out of non-wood material.

Both designs use a simple chassis that is a rectangular box in order to conveniently have access to the electronic systems of the robot. In addition, the rectangular box is hollow in order to reduce weight and leave room for the 1.5-kilogram weight that will be carried on board. The drive train will attach to the chassis in order to ensure the robot can be held together. Design 1 (Figure 16) takes advantage of wheels in order for the weight to be light and the frame to be rotatable in order to climb stairs. The front wheels are attached in order to maximize surface area contact with the stairs. Each wheel is also independently powered in order to allow “full-wheel drive” and generate torque when the wheels are in contact with any surface. The back wheel does not rotate since having all sets of wheels rotatable will make the robot unstable when climbing over multiple stairs. The back wheel is meant as an extra surface to ensure the robot will not fall backwards. This design will require an additional H-bridge, axles, and two motors in comparison to Design 2 (Figure 11).

The files for Design 1 (Figure 14) is specifically as follows:

Axel and Wheels

- Axel.ipt
- Front Wheel Base.ipt
- Rear Wheel Base.ipt
- Wheel Inner Ring.ipt
- Wheel Inner Spacer.ipt
- Wheel Main.ipt
- Wheel Outer Right.ipt

Vehicle Panels

- Vehicle Bottom Panel.ipt
- Vehicle Front Panel.ipt
- Vehicle Rear Panel.ipt
- Vehicle Side Panel.ipt
1. Axel and Wheels

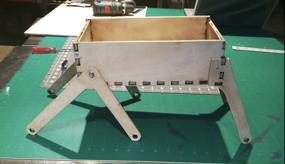
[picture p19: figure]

Figure 15 - Design 1: Prototype Side View

38 | P a g e

In addition, a prototype cutout was made for Design 1 (Figure 15). This was cut out of birch wood to show that the design was technically feasible.

Design 2 is still in development, but Figure 11 shows a mostly completed CAD assembly. Design 2 (Figure 11) mainly differs from Design 1 (Figure 15) in that it will require more than 6 feet of track as opposed to 6 wheels. The track will be powered by 4 motors (2 on each side) in order to supply enough torque. The traction problem is also solved by having a continuous surface in contact with the stairs, albeit in a less flexible shape than Design 1 (Figure 15). The gear design will also provide greater torque to the robot’s drivetrain since the speed will be reduced. Design 2 will require fewer electronics components (as stated above) but will require more material and potentially stronger motors in order to work.

Simple Machines

Design 1 (Figure 15) features a lever for the front 4 wheels and a wheel and axle for each of its 6 wheels. The second-class lever will get its force from when the wheels apply a force to the stairs and the stairs push back. This will cause the level to rotate around the fulcrum, which is on the robot chassis, and allow the wheels to climb up the stairs and bring the robot with it. This is a simple machine since the force from the stairs pushing back moves the robot, causing work to be done. The wheel and axle machines found on each of the 6 wheels allow a motor to spin each wheel and axle at the same rate in order to cause the robot to drive. The wheel and axle are simple machines on this robot since they apply a force (from the motors) to move the robot and spin themselves. In combination with the lever on the front wheels, the robot will be able to climb stairs since the wheels can move the whole robot and the level will allow the robot to rotate in order to climb stairs.

Design 2 features gears that are used to power the tracks. The tracks will lay into the gears (of two different ratios) in order to supply maximum torque when the robot is climbing up the stairs. Torque is important in order to overcome gravity and climb up the stairs, meaning the gears are designed to be slow but powerful. It is a simple machine because it helps the robot apply a force coming from the motors against the ground in order to do work to get up the stairs.

The main reason there are two designs is so that we can test the functionality of these two simple machines. Design 1 (Figure 15) uses more machines in order to increase the surface area and power applied to the surface through its lever and wheels. Design 2

(Figure 11) uses gears to provide torque to the track but has a smaller surface area by being unable to rotate. As both designs are tested, there will be much emphasis placed on how the design of the simple machines will affect the robot performance.

40 | P a g e

## Technical Design Report

Major Changes

The design that incorporated two independent pairs of rhomboid tank treads was reconsidered due to time and material restraints. Ultimately, the group decided that this design would most likely be too costly and complicated. From there the mechanical team split into two different groups. One of these groups designed a robot that utilized a single pair of large trapezoidal tank treads, with two motors powering each tread. The second team designed a robot that utilized six independently powered and controlled wheels attached to stilts that separate them from the chassis. Two pairs of wheels would be connected together at the front of the robot and would be attached to the chassis via an axle that allowed the wheels to rotate around the surface of the stairs. The rear pair of wheels were rigidly attached to the chassis. When each design had been completed we analyzed them as a team to determine which to pursue. Though it was difficult to tell which would perform better at climbing stairs, our team decided that the production of treads for the tank design would be prohibitively time consuming compared to the wheeled design. In addition, the tracked design would require more power and more weight than the wheeled design, ultimately deciding the wheeled design would lead to a better outcome.

Having agreed upon the wheeled design it was prototyped and tested it. During the design iterations several important changes were made. Our first prototype did not have sufficient power to climb the stairs. To remedy this we first replaced our initial small 9 volt DC motors with similar but much more powerful ones. These new motors were 12 volts and ran at 30 RPM or 100 RPM. Secondly, the second prototype chassis was constructed out of acrylic, as opposed to the wood in the first design. This was done to save weight and reduce the amount of torque needed to pull the robot up the stairs. In our third design iteration we added braces to the two forward axles to reduce flexing that caused the wheels to lock up. In addition, after several of our axles snapped we designed new stronger axles that were able to withstand the stress of going up stairs. Springs were also attached to the front-most section of the robot to pull up the robot after the front wheels ran into a flight of stairs. These major changes are what have allowed the robot to improve from being unable to even move up a slight ramp to reliably climbing stairs.

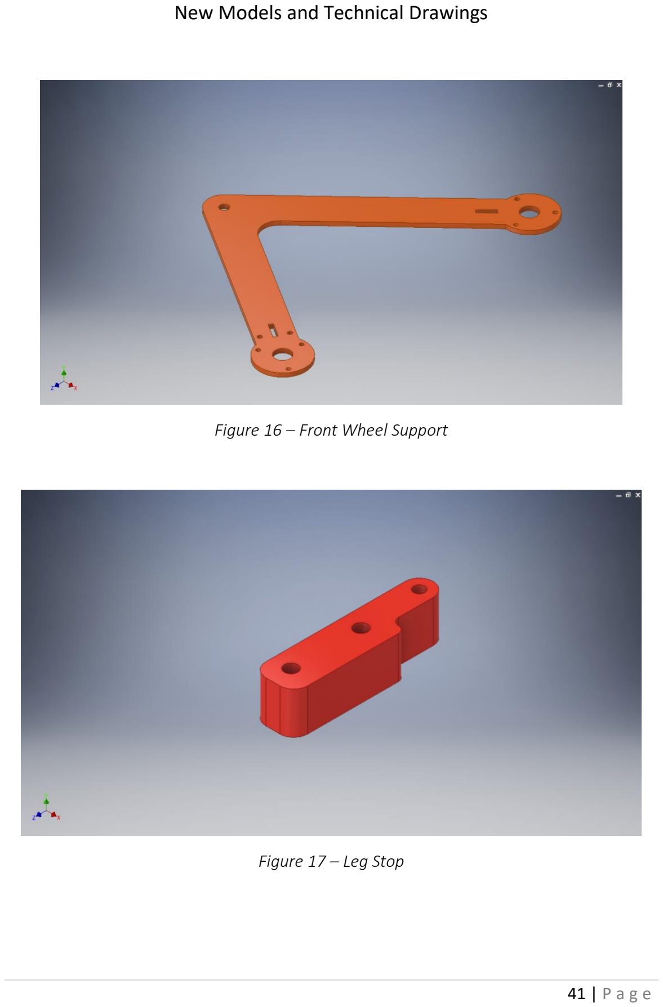
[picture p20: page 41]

New Models and Technical Drawings

Figure 16 – Front Wheel Support

Figure 17 – Leg Stop

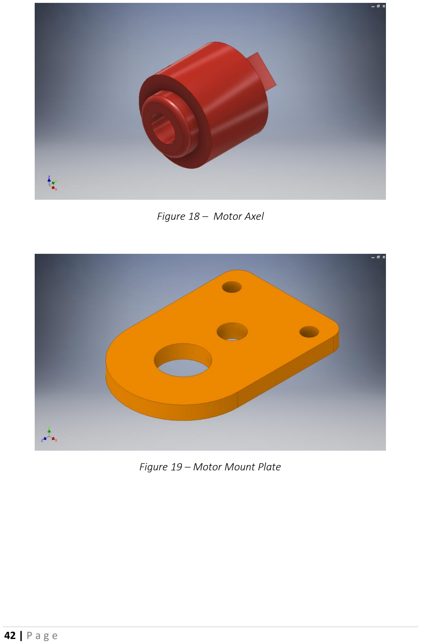
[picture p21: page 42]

42 | P a g e

Figure 18 – Motor Axel

Figure 19 – Motor Mount Plate

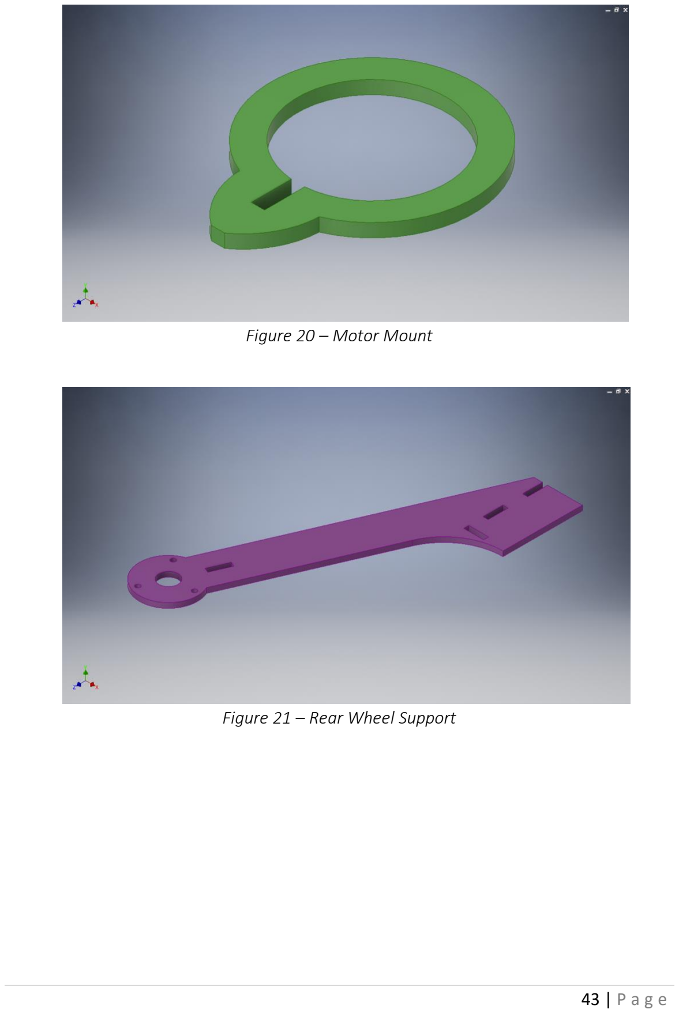
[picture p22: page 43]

Figure 20 – Motor Mount

Figure 21 – Rear Wheel Support

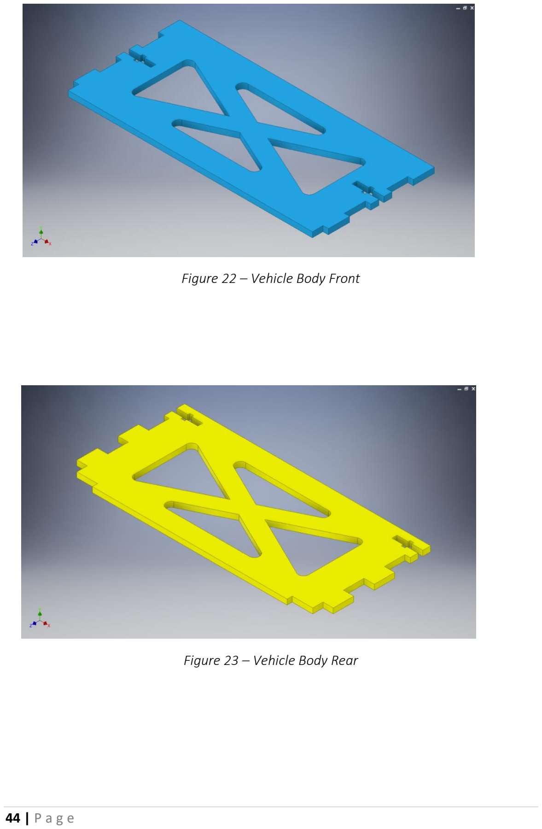
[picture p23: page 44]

44 | P a g e

Figure 22 – Vehicle Body Front

Figure 23 – Vehicle Body Rear

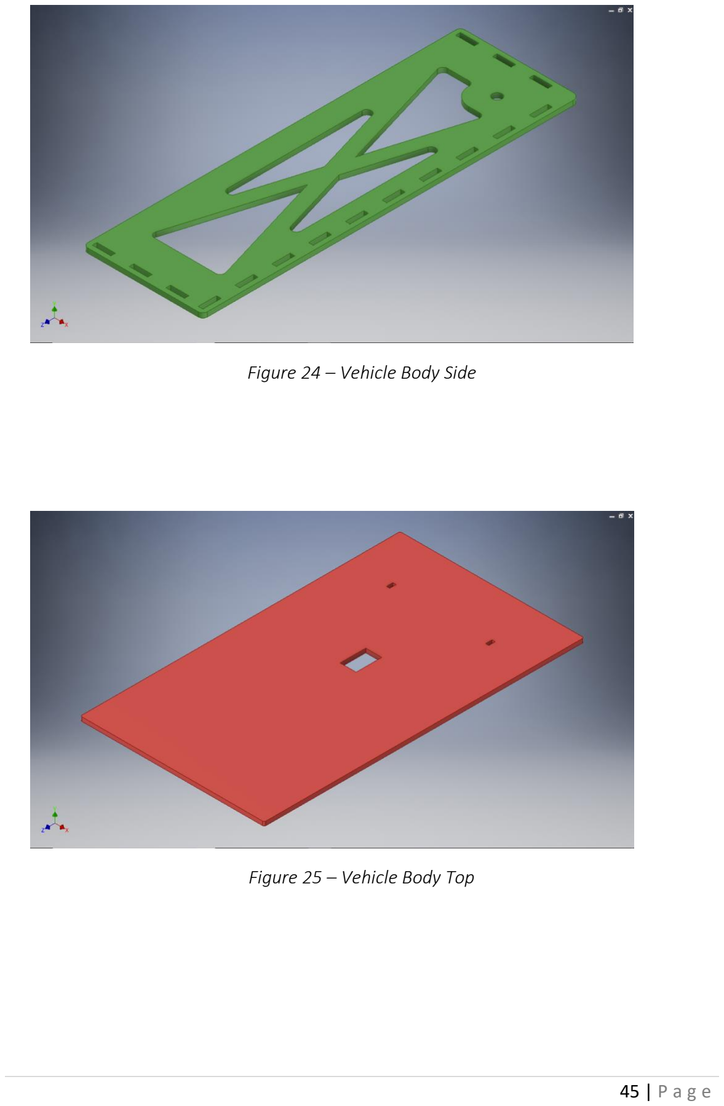
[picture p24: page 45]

Figure 24 – Vehicle Body Side

Figure 25 – Vehicle Body Top


46 | P a g e

Figure 26 – Wheel Main

Figure 27 – Vehicle Body Bottom

Final Design


Figure 27 – Finished Design


Figure 28 – Finished Design on Stairs


48 | P a g e

Figure 29 – Front View on Stairs

Figure 30 – Side View on Stairs

Challenges Faced

Some of the primary challenges we faced during the creation of the robot arose due to monetary and time constraints. In the process of designing our robot we considered multiple designs that incorporated a continuous track or tread. The most time efficient way of creating such a robot would have been to purchase a manufactured tread or belt, 3D printed tracks would have taken too long to print and assemble. Unfortunately we could find no belts of appropriate specifications that would left room in our budget for other important components. Had we the time to print all the necessary track or the money to purchase tread we could have more seriously considered using a tracked robot. Other obstacles also increased the challenge that time posed. One example of this was our reliance on the Dabble Lab. Several times throughout our build process equipment failure meant we would lose a day of work time. Conflicting schedules meant we could often only meet a couple times in a week, meaning a delay of just a day could put us more than half a week behind.

Overcoming these challenges meant adapting our design methods and time management. During our initial design phase we had to take a close look at the feasibility of each proposed design. While the tracked design certainly had its benefits over some of the others, ultimately we determined it to be an unrealistic design path. For all its pros it was simply too time consuming to pursue. To save resources and time we stopped our prototyping of tracked designs and put all our effort into producing a functioning prototype that used wheels. Doing this allowed us to fast track our primary design while minimizing waste on designs we couldn’t reasonable build. Time management was also vital in keeping our team on track to complete the robot within the set time constraints. We began to anticipate the possibility of equipment failure. When we planned work sessions we would often set a backup time in the event we couldn’t use the required equipment for progress. We also extended the length of our work sessions to make up for time we had lost previously and to negate the effect of future delays. By proactively responding to these obstacles we have been able to complete our robot on time and within budget.

50 | P a g e

Reflections

Reflection 1

1). What major are you pursuing, and what got you interested in that topic?

I’m pursuing two majors with two degrees: Informatics and Anthropology. I’ve found my interest in creating things since I was very young. I made my parents holiday presents by hands every year. I started my design journey at making mini wood crafts at the age of 6. At that time, I thought I would be an architect in the future. However, my design interest in building real construction was killed in my first semester of high school by the fact that I did not enjoy physics. But I still enjoy the design process. So I moved on to another field of design, chemical engineering, and bioengineering, hoping to design some new formulas. My second try failed quickly after two semesters of labs. It was partially because I didn’t get to talk to many living creatures, as known as people, and I didn’t feel the lab environment was encouraging creativity. Luckily, my third shoot worked out. After two semesters of “social isolation,” I started researching different modern social networking mobile applications and computer software. I then found that although those apps had the same purpose of communication, their design made my user experience very different. I then did more study on the idea behind those designs. This is the moment that I knew where to place my design enthusiasm. However, I still felt like my puzzle was incomplete. I found the missing piece from an Anthropology class where we discussed the human nature, such as value. I always believe that good design helps to improve our living quality through unconsciously introducing it’s embodied values. And my interest is to become a good designer who can do good designs with good values. So my current interest is in HCI, information architecture and information assurance and cybersecurity, as well as what is the role of technology in globalization and how does it help shift human’s culture. – Rhea

I am pursuing a major in mechanical engineering. I can’t remember when I decided on
specifically mechanical, but I have always been interested in engineering of some sort or another. In the middle of high school, I decided that I wanted to become an astronaut, so I was going to study aeronautical engineering. Then later on, I had a change of heart, when I realized that it would be much better to try and fix the issues on our own planet. From that point, I was really interested in biomimicry and how it can combine with engineering and architecture. Now, I am interested in pursuing robotics, as I have just had that avenue opened up to me and
it is really exciting, as unfortunately my high school never offered any robotics, so I am having
to make up for lost time. - Caelen

I am majoring in Computer Science and Engineering. In high school I took a web design class and got introduced into web programming, and from there I started to learn other programming languages and joined different engineering clubs. I enjoy working on computers, since they are accessible, powerful, and it doesn’t “cost” anything to write code. - Aaron

2). What do you think working as an engineer means?

Engineers are designers who focus on designing practical solutions. So engineers are just like designers— they can work in various fields. I think working as an engineer means that I’m only a part of the project team and I need to learn how to collaborate and communicate to achieve the design goal.

An engineer should be able to analyze, design, develop, test, and evaluate the design object with creativity. However, I think engineers usually focus more on improving and maintaining the current system than on building something new from nothing. I think each engineer is responsible for being creative and realistic on each design project to make sure the design has a practical use. I think engineers are meant to perceive the world underlying mathematical and mechanistic basis, and remodel the world using quantitative tools. Engineers should know some science and have the ability to draw connections between science and the practical use. Engineers are ambassadors who bridge science and everyday life by applying science to design. And those applications of science in engineering can later help advance science. Engineers are craftsmen who realize their ability and potential in solving problems in different field such as healthcare, transportation, food, education, communication, and the environment. I think scientists focus on finding the fact of the reality, while engineers are dedicated to building new reality based on current reality, and they ultimately make this world a better place together. - Rhea

I think that being an engineer is being someone who can be presented with a problem,
whatever their specific field is, and using creativity and scientific knowledge to find a solution
for it. It means working with a team to create a completed product or project. - Caelan

Working as an engineer means applying skills and knowledge to solve a problem, as well as learning new skills and obtaining knowledge as you work. From engineers I have talked to, they always strove to gain hands-on experience and learn skills as they work on projects or solve problems. Engineers also have to be willing to admit when they don’t know a certain topic and have the attitude that they will learn as much as they can about a topic. – Aaron

3). What are the most important skills for an engineer to have?

I think the first important skills for an engineer to have is communication skill. Based on scientific research, creativity is the innovative outcome of a collective community. According to my observation, an engineering project usually has a big team but still takes a long time to finish. Although prototyping reduces some cost in the engineering design process, inefficient team communication can promise a smoother collaboration experience. So I think the ability to work as part of a team is essential for an engineer. The prerequisite for being an engineer is having a solid foundation of knowledge in STEM fields at a certain degree level, such as a master degree. So I think having a qualification in STEM subjects can endorse an engineer’s problem-solving skill in solving mathematical and logistical problems. It would also be great if an engineer has a strong analytical skill so that the solution can be developed at a lower risk of failure. I believe one’s analytical skill can be built out of quantity, as being said, “quantity makes quality.” Since engineering projects are usually very complex, it’s good if engineers can always pay attention to details during planning, designing, and construction processes. I think attention and sensitivity to detail is one important skill for an engineer to have for reducing the chance of project abortion. Additionally, I believe a good engineer should also have excellent communication skills in using technical terms in at least one language, and be able to talk to people with different knowledge background, such as clients. - Rhea

First and foremost, creativity. An engineer, of any field, needs to be able to think outside of the
box, they need to be able to look at the problem from many different points of view. Secondly, they need to have a good understanding of scientific principles relating to their field. - Caelen

52 | P a g e

The most important skills for an engineer are teamwork and desire to learn. Engineers will not be experts in everything required to solve a problem, so they need to be able to work with other people who know more about another topic than they do. Engineers also need to be able to lead the project forward with their own knowledge. While the team is working together, engineers should also want to learn from each other in order to improve their own knowledge and understanding so that they can be successful in future engineering projects. – Aaron

4). What do you hope to get out of this class?

Learn how to communicate with engineers and also learn some skill. Be empathy instead of sympathy. Since anything working environment requires team communication and collaboration skills, I want to practice my skills in the engineering environment. I want to practice my skills in professional planning, communicating, and collaboration with engineers. I want to better understand what and how engineers think and build empathy with them. So I want to pick up some practical engineering skills which can allow me to prototype my idea in new ways. I want to learn the newest technology in the industry such as using CAD software, 3D printer and Laser cutter for prototyping. I also want to learn more project management skills and apply them to everyday life and my future projects. For example, I already applied Gannt chart at managing my school schedule and moving plan. I believe this class can help me build much more other basic skills that are often ignored but essential for my future career development. In the meantime, I want to practice my knowledge from other fields in engineering. For example, I can practice my design thinking skill from designing information system. By taking this intro engineering class, I can see how I feel truly feel about engineering at the age of 20. Moreover, I want to make friends at different ages with diverse backgrounds. – Rhea

I hope to enjoy myself in this class, I want to make sure that I’m not overly romanticizing what
being an engineer is, but I don’t think I am. I think an important part of this class will definitely
be working as a cohesive team, not only so that our project succeeds, but also so that we all
have a good time in this class. – Caelen

I hope to learn skills that are related to fields of engineering outside my major. This includes mostly electrical circuits, CAD modeling, 3D printing, and laser cutting. I don’t want my education to be one-dimensional (only learning programming) so I feel it is important I take this class in order to introduce me to ways I can become a more well-rounded engineer. – Aaron

Reflection 2
1). What do you think will be your greatest challenges in working on this project and why?

Stay positive is my greatest challenges in working on this project. I am not an expertise in the domain of our “stair-climbing robot” project, so I’m afraid to give feedback, ask questions and share my idea. Also, it’s a challenge for me to stay positive while the team has a negative patter, “Yes, looks good.” The challenge here for me is that I will be discourage if I will not be the one who is still willing to share ideas while having no feedback. Also, asking question in the domain that I’m not very good at makes me feel extremely uncomfortable. It’s a challenge for me to keep motivated for what I’m learning. Since this class is an intro class, I’m afraid that my teammates are not taking it seriously. I’m very sensitive to the environment and I will also lose my interest in the class, and therefore will not do as great as I wish. Also, staying positive is even harder when I don’t know my teammates that well. All in all, that’s why I thinking keeping a positive is my greatest challenge in this class. - Rhea

One of the greatest challenges that I have been facing is working well as a team with all of the members. Most of the team I can work with well, but there are a couple that I am having a hard
time working with. Some of the issue arises from both sides being stubborn and not fully listening to each other. - Caelen

My greatest challenge will be finding ways to get everyone to contribute as well as balancing my contributions in this class with my other classes. Time is getting more and more precious and limited, so we need to make sure the project is finished on time. Not only that, we have to make sure everyone in the group is learning and contributing, as otherwise the group will not work well. - Aaron

The greatest challenge for this project will clearly be that the robot is able to climb up a set of stairs. The main problem in this area is to enable the robot to push itself up the stairs without its contact points slipping down. This is the greatest challenge because if the robot slips down the stairs, then it would never be able to move up a set of stairs. - Valentina

2). What steps are you going to take to ensure that you will be successful in this class?
Try to add be not afraid of asking stupid questions even if I don’t know too much about those physics concepts. Even if when I don’t know how to phrase my question due to the language barrier, I should still ask as many questions as I can in order to understand the problem statement correctly and therefore engaging in project deeply. Getting my hands dirty is the second thing I will do. I will try to prototype more. I have learned that prototype is not meant to be perfect, and it is the best way in the design process to find out if a design idea works. Even if the prototype has the lowest fidelity, I should still externalize my idea into a prototype. Additionally, I will communicate well with my teammates to make sure we are on the same page. I will try to make my problem statement as clear as possible, and ask explicit questions, for example, “I am not aiming at solving the problem of ….” I will try to critique as much as I can with valuable feedback. – Rhea

I endeavor to maintain a good team mentality, and make sure that I do my best to listen to all
sides of an argument. I try my best to offer as much constructive criticism as possible. Also, I
have been making sure that I do my share of the work and do everything that I say that I will in
a timely manner. – Caelen

I am trying to balance my workload with other classes in order to make sure I can contribute to my group’s project. This also means researching things on my own and spending time outside of class improving my engineering skills. I am also trying to teach what I already know to the rest of my group in order to incorporate them more. Finally, I am trying to talk to course staff more, and I believe they have helped me become better engineers. – Aaron

Put more effort in my involvement in the design process. I don’t particularly know much about programming and CAD design, however we have learned the basics during class, so in oder to contribute on the success of this project I will take time outside classes and the lab times to practice on my own programming and OnShape design. I would also ask for help whenever I need. There are a lot of skillful members in my group and they are always available to help and explain how to do something. – Valentina

3). Teamwork is a very important skill for engineers, you will rarely be working on a project alone. What steps are you taking to ensure your team as a whole will be successful?

54 | P a g e

Communication is the most important part in the team work. I will take the role of a facilitator to make sure the communication of idea is going smoothly throughout the project. I will also learn how to use professional project management tools to help us better manage the overall project. I will be specific in the communication process and try to make professional statement. I will help assign the work fairly and everyone stays happy. Also, I will make sure everyone’s on the same page so that we are aiming for a same goal. This means, everyone understand the problem statement correctly, and then critique on the solution idea. I will schedule a weekly critique for our group so that our team have a block of two hours outside the class meeting, and give valuable feedback. I hope I can be the one who introduces a positive pattern in the team. - Rhea

Communication is key, making sure that all of the team is informed as to what our plans are,
what everyone’s jobs are and when are key deadlines. Also, making sure that each member is
given projects that they can do, both based on their skills and time availability. Also, it is very important to make sure that the criticisms that you give are constructive, as it is a team and you
want everyone to succeed together. - Caelen

I am making sure that the team is fully involved, engaged, and up to date on what needs to get down. I also try to make sure team members are playing to their strengths while letting them experiment with things outside of their comfort zone. Ultimately, I am trying to keep everyone on track while also making the project fun and educational. - Aaron

Create an environment in which people feel comfortable taking reasonable risks in communication and defending their position even when is not the common one.
Practice 'Participatory Leadership': assigning tasks, evaluating progress, and offering guidelines for the team to function as a whole.
Each member is committed to get the best out of himself, to put all their effort to get the job done. The commitment of the group makes it happen to a high performance team where the sum of the parts multiplies. - Valentina

Reflection 3

1). What have been your greatest challenges so far working on this project?
Trying to apply my limited physics knowledge on the mechanical part of the project has been one of my greatest challenges. Since I haven’t touched physics for at least two years, it’s been a hard time for me to pick up that memory and apply that knowledge while connecting those circuits. The problem becomes even more challenging when I realized the gap between the ideal circuit graph and the actual position on the breadboard. – Rhea

One of the biggest challenges was getting the team to all work together, as for a long while
there were two different designs in our group. Luckily our group finally settled on one design
and so we are now a united front. - Caelen

The greatest challenges so far is overcoming our weaknesses, primarily the team’s lack of knowledge about circuits. The electrical team has done a lot of work to learn electronics, but we still do not see the same progress the mechanical team has. Other than that, building our working prototype has been difficult since we are unsure of how the design will work. – Aaron

For our project the greatest to challenges have been deciding whether the want wheels or tracks in our robot, and the electrical and circuit part. The first challenge revolves around which one is better for the task of moving up stairs. The second challenge I thinks is the greatest because our schematic is very complex and we need to put to work 6 motors, and these are our only parts. We have a lot of parts so it will be very hard to install them. - Valentina

2). Has completing your project been more or less challenging than you expected? Why?
The project goes pretty well so far and has been less challenging than I expected. I expected the Arduino part and the electrical part would be very hard for me to understand the concept. However, I found that Arduino coding is fairly intuitive and manageable for me to handle it. So I might be able to implement the Bluetooth remote control at the end of the project. – Rhea

Completing my section of the project has been just as challenging as I expected it to be, after I
changed my design from a tracked robot to a wheeled robot. I was initially really surprised by
how hard it was to create a system of tracks. - Caelen

Completing the project has gone pretty much how I expected, since I had prior experience with robotics and know generally what the process was like. Prototyping has been a little slow, but that is acceptable since we still have time left. That being said, I was unsure how everyone on the team would work together, and I was surprised that we have worked well as a team. I also thought the mechanical part of the design would be challenging, but two members of the team know CAD very well. So, I would say completing the project has gone fairly well overall. - Aaron

In general printing and laser cutting the parts has not been challenging at all. However I believe that the most challenging part of the whole project is the electronics. I was definitely harder that I expected it was going to be and is visible on the schematic. There are a lot components and interconnections in the circuit and we need to be careful the we don’t make any mistakes that may affect the robots ability to move around. - Valentina

3). Do you think the goals you set for your project in your proposal are still realistically achievable? Why or why not?
I think the goals I set for my team project in the proposal are still realistically achievable because our goals are set on a feasible conditional which gives us time to focus on our main goal. The mechanical team has made great progress in prototyping our robot. I have enough confidence in our robot successfully climbing up stairs in Area 01 with wireless control. – Rhea

Most of the goals that we set for our project are still achievable, the one that I am not sure of
right now is to carry a 1 kg weight up the stairs. As of right now I don’t know if this will be
possible, as the motors might not be able to push it up the stairs. - Caelen

The goals we set are still realistically achievable, with the exception of climbing the chosen set of stairs. We should still be able to drive on a flight or inclined surface as well as carry an additional weight. The main challenge will be climbing our chosen flight of stairs given the size of our wheels. This may force us to change our goals and instead choose a shallower set of stairs. We will not know this until we prototype however. - Aaron

In my opinion the goals set by our team are achievable. We set goals that at our reach and that easy enough to be achievable but hard enough to challenge us. They are realistically achievable because we

56 | P a g e

adapted them to what we have at our reach, we are going to focus on only a set of stairs for the start of the project, however we hope it could be applied to any other type of stairs, we are also making sure that our project works in a specific environment so that then it could be modified to a different one. -Valentina

4). What skills or information do you need to help you finish your project?
I need to self-learn more Arduino commends in order to give our robot the ability to complete more tasks. Also, I need the knowledge of troubleshooting the problems that might occur in our future prototype testing. The last skill that I might want to for completing this project is how to utilize those machines in making our robot looks nicer than it's current look. – Rhea

As of right now, most of the skills that we need have already been addressed. Moving forwards,
we will be finishing the full assembly of the vehicle and working on making sure the code works
to properly drive the vehicle upstairs. – Caelen

We need to build a bluetooth application and figure out how to communicate over bluetooth with our robot. We also need to start prototyping to see if we can overcome our chosen flight of stairs or perhaps choose to build our own. Other than that, some softer skills we will need are to just stay motivated and keep our teamwork up. - Aaron

Because our robot will be controlled by bluetooth, we need more information in how to configure it. It is not hard, however we need to know how to do it correctly to ensure that it will work. It is also necessary more help on how to install all the electronic parts of the robot. Because it is a very complex project in that specific area, it is necessary more skills. - Valentina

## Reference

- Sharma G. (2009, May 23). Conveyor belt based sorting machine object size detection
east | chandigarh. | Retrieved | 12 | March | 2018 | from
https://www.youtube.com/watch?v=ThhZDGRrlLs.
- UPHIGH Productions. (2016, May 02). Robot Kitchen - Behold The Future. Retrieved 11 March 2018 from: http://www.youtube.com/watch?v=rNcPVvIs_tk.
- NBC News. (2017, January 04). Introducing Kuri, The Home Robot. Retrieved 11 March 2018 from: https://www.youtube.com/watch?v=QsxmZPRhlsc.
- FarmBot.io (2016, June 30) Introducing FarmBot Genesis. Retrieved 11 March 2018 from: https://www.youtube.com/watch?v=8r0CiLBM1o8
- Transcend Tactical (2017, Nov). Introducing the first hassel-free Tactical Robot. (n.d.). Retrieved 11 March 2018 from: https://transcend.ai/business-units/public-safety/law-enforcement/
- Automation and Control Technology Final Year Project. (2014). YouTube. Retrieved 11 March 2018, from https://www.youtube.com/watch?v=Q1lf14W2sSE
- Base of Support. (2017). Physiopedia. Retrieved 12 March 2018, from https://www.physio-pedia.com/Base_of_Support
- Continuous Tank Treads by whowhatwhere. (2010). Thingiverse.com. Retrieved 12 March 2018, from https://www.thingiverse.com/thing:2820
- Friction and Friction Coefficients. Engineeringtoolbox.com. Retrieved 12 March 2018, from https://www.engineeringtoolbox.com/friction-coefficients-d_778.html
- Gupta, R. (2015). STAIR CLIMBING ROBOT. researchgate.net. Retrieved 12 March 2018, from https://www.researchgate.net/publication/303549760_STAIR_CLIMBING_ROBOT
- Heriot-Watt EPS Mechanical Engineering (2011), Stair climbing Robot Shrimp 2011.
YouTube. | Retrieved | 12 | March | 2018, | from
https://www.youtube.com/watch?v=4QDJWIUDSEk
- Robotpark ACADEMY (2013). How to Design a STAIR CLIMBING ROBOT 81004 -
Robotpark | ACADEMY. | Retrieved | 12 | March | 2018, | from
http://www.robotpark.com/academy/how-to-design-a-stair-climbing-robot-81004/
- Lucidarme, P. (2008). B2P2 robot climbing stairs. YouTube. Retrieved 12 March 2018, from https://www.youtube.com/watch?v=3I_KoCeAdEw

58 | P a g e
- Mohan, A. (2014). Rocker-Bogie Mechanism. YouTube. Retrieved 12 March 2018, from https://www.youtube.com/watch?v=bP7p5Bd2d50
- Planetary gear by ngoodger. (2014). Thingiverse.com. Retrieved 12 March 2018, from https://www.thingiverse.com/thing:264769
- Stair Climbing Mobile Robot - ARTI: Rugged Commercial Platform. (2016). YouTube. Retrieved 12 March 2018, from https://www.youtube.com/watch?v=sohpgx6j_lk
- Stair Climbing Robot. (2011). YouTube. Retrieved 12 March 2018, from https://www.youtube.com/watch?v=OdJpDXZEkU0
- Stair Climbing Robot. (2015). Instructables.com. Retrieved 12 March 2018, from http://www.instructables.com/id/Stair-Climbing-Robot-1/
- Stair Climbing Robot - SM.mp4. (2011). YouTube. Retrieved 12 March 2018, from https://www.youtube.com/watch?v=3qWYAOGZVM4
- Stair climbing robot (Triple Bended Crosswheels). (2013). YouTube. Retrieved 12 March 2018, from https://www.youtube.com/watch?v=hBFf0pZjY94
- Stair Climbing Robots and High-Grip Crawlers | InTech. (2010). YouTube. Retrieved 12
March 2018, from https://www.youtube.com/watch?v=dgJ1nHu-hOo

Yap, K. (2017). Stair-climbing Robot. YouTube. Retrieved 12 March 2018, from https://www.youtube.com/watch?v=FuJdlcaUd8A

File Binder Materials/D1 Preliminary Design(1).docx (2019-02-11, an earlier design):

Aaron Su

Caelen Coe

Noah Whelan

Mahamed Dirie

Rhea Chen

Valentina Valero

# Preliminary Design

### Electrical System Schematic

<Insert at end of lab>

Technical Drawing

No major changes have been made since the previous Technical Drawing Section. Please refer to Concept Design section “Preliminary Technical Drawings” and figures 5-10 for all technical drawings.

### Digital Models


Figure 2: Design 1, Isometric View of Parts


Figure 2: Design 2, Isometric View of Parts

Both designs are assembled and can be seen in Figure 1 for Design 1 and Figure 2 for Design 2. Design 1 and Design 2 will both take advantage of laser cutting when possible in order to save time and PLA material. This means the panels of the chassis, wheels (Design 1), supports for drive train (Design 1 and 2) and sprockets (Design 2) will all be laser cut. Smaller pieces, such as the axles in Design 1 and individual tracks on Design 2 will be 3D printed in order to be accurate and be made out of non-wood material.

Both designs use a simple chassis that is a rectangular box in order to conveniently have access to the electronic systems of the robot. In addition, the rectangular box is hollow in order to reduce weight, and leave room for the 1.5 kilogram weight that will be carried on board. The drive train will attach to the chassis in order to ensure the robot can be held together.

Design 1 takes advantage of wheels in order for the weight to be light and the frame to be rotatable in order to climb stairs. The front wheels are attached in order to maximize surface area contact with the stairs. Each wheel is also independently powered in order to allow “full-wheel drive” and generate torque when the wheels are in contact with any surface. The back wheel does not rotate since having all sets of wheels rotatable will make the robot unstable when climbing over multiple stairs. The back wheel is meant as an extra surface to ensure the robot will not fall backwards. This design will require an additional H-bridge, axles, and two motors in comparison to Design 2.

The files for Design one are specifically as follows:

Axel and Wheels

- Axel.ipt
- Front Wheel Base.ipt
- Rear Wheel Base.ipt
- Wheel Inner Ring.ipt
- Wheel Inner Spacer.ipt
- Wheel Main.ipt
- Wheel Outer Right.ipt

Vehicle Panels

- Vehicle Bottom Panel.ipt
- Vehicle Front Panel.ipt
- Vehicle Rear Panel.ipt
- Vehicle Side Panel.ipt


Figure 3: Design 1, Prototype Side View

In addition, a prototype cutout was made for Design 1 (Figure 3). This was cut out of birch wood to show that the design was technically feasible.

Design 2 is still in development, but Figure 2 shows a mostly completed CAD assembly. Design 2 mainly differs from Design 1 in that it will require more than 6 feet of track as opposed to 6 wheels. The track will be powered by 4 motors (2 on each side) in order to supply enough torque. The traction problem is also solved by having a continuous surface in contact with the stairs, albeit in a less flexible shape than Design 1. The gear design will also provide greater torque to the robot’s drivetrain since the speed will be reduced. Design 2 will require fewer electronics components (as stated above) but will require more material and potentially stronger motors in order to work.

### Simple Machines

Design 1 features a lever for the front 4 wheels and a wheel and axle for each of its 6 wheels. The second class lever will get its force from when the wheels apply a force to the stairs and the stairs push back. This will cause the level to rotate around the fulcrum, which is on the robot chassis, and allow the wheels to climb up the stairs and bring the robot with it. This is a simple machine since the force from the stairs pushing back moves the robot, causing work to be done. The wheel and axle machines found on each of the 6 wheels allow a motor to spin each wheel and axle at the same rate in order to cause the robot to drive. The wheel and axle are simple machines on this robot since they apply a force (from the motors) to move the robot and spin themselves. In combination with the lever on the front wheels, the robot will be able to climb stairs since the wheels can move the whole robot and the level will allow the robot to rotate in order to climb stairs.

Design 2 features gears that are used to power the tracks. The tracks will lay into the gears (of two different ratios) in order to supply maximum torque when the robot is climbing up the stairs. Torque is important in order to overcome gravity and climb up the stairs, meaning the gears are designed to be slow but powerful. It is a simple machine because it helps the robot apply a force coming from the motors against the ground in order to do work to get up the stairs.

The main reason there are two designs is so that we can test the functionality of these two simple machines. Design 1 uses more machines in order to increase the surface area and power applied to the surface through its lever and wheels. Design 2 uses gears to provide torque to the track, but has a smaller surface area by being unable to rotate. As both designs are tested, there will be much emphasis placed on how the design of the simple machines will affect the robot performance.

### Updated Bill of Materials

No major changes have been made since the previous Updated Bill of Materials Section. Please refer to Concept Design section “Updated Bill of Materials” and “Table 1: Updated Bill of Materials Table”.

ENGR202 – Winter 2018 Team 9

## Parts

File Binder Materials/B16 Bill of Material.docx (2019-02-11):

Table 2 - Bill of Materials Table

Part Name | Quantity | Price (per individual item) | Link
Gearbox Motor (or something similar) | 6 | ~5.83 | https://robokits.co.in/motors/30rpm-metal-gearbox-motor?cPath=2_3& (http://robotechshop.com/shop/robotics/motors/dc-motors/yellow-gearbox-motor/?v=7516fd43adaa)
Qunqi L298N Motor Drive Controller Board Module Dual H Bridge DC Stepper For Arduino (H Bridge) | 6 | $6.89 | https://www.amazon.com/dp/B014KMHSW6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 (https://www.amazon.com/dp/B014KMHSW6?creative=395033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)
Arduino Uno REV3 | 1 | $22.00 | https://store.arduino.cc/usa/arduino-uno-rev3
Arduino Uno Shield Terminal | 1 | $14.95 | https://www.adafruit.com/product/196
Springs | 6 | $1.30 | http://www.centuryspring.com/extension-spring-5986.html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
6 sq. ft. birch 3-ply | 2 | $0.63 | https://woodcrafter.com/plywood-squares/?gclid=EAIaIQobChMI2bL2rfjg2AIVUYJ-Ch0L9gHZEAYYASABEgJ7EvD_BwE
5" Wheel (4-pack) | 6 wheels | $5 per wheel | https://www.vexrobotics.com/edr-wheels.html
12 Volt battery | 1 | $20 | https://www.google.com/shopping/product/8734525288015090628?lsf=seller:1221574,store:14014099157399252682&prds=oid:16521898599169375518&q=12+volt+battery&hl=en&ei=y7trWqniO4K2jwOLpJzwDw&lsft=ref:212,loc:1&lsft=gclid:Cj0KCQiAwKvTBRC2ARIsAL0Dgk14oLNiVGxuOJuLvlef2p6x44mD-dyN_Z8Voc53cXyUgqYMmJ4XHVUaAu2eEALw_wcB
Spool of 3D printing filament | 1 | $22.74 | https://www.matterhackers.com/store/l/thriftymake-black-pla-filament-1.75mm/sk/MNEGU7WQ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
Bluetooth Receiver | 1 | $6.95 | https://www.alliedelec.com/adafruit-industries-1501/70460944/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
Accelerometer | 1 | $9.95 | https://www.sparkfun.com/products/12786?_ga=2.167625022.1068696171.1516262647-508659819.1515111507

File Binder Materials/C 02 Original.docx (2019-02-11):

Aaron Su

Caelen Coe

Noah Whelan

Mahamed Dirie

Rhea Chen

Valentina Valero

# Design Concept

### Design Requirements

The project will be a bluetooth-driven, stair-climbing robot. The robot will be capable of climbing stairs of which each step is 5 inches tall and 12 inches long through a multi-wheeled design. The robot will also have to pull up a 1.5-kilogram weight, making the design of the robot light and sturdy but also requiring independently driven wheels. Finally, the robot will have to have its own power source and Arduino in order to be controlled over bluetooth.

User Interface

The main users of the project will be staffs or drivers who will control the robot to travel to a desired destination, either with or without cargos. Our users are intended to have similar skill and ability as actual users of a commercial stair-climbing robot, such as security officials, military officers, or professional movers. Considering our users’ diverse cognitive affordances, such as language, and education background, we will implement our user interface on either a tablet or on a remote controller, with buttons labeled with universal symbols and colored in shared convention (Figure 1, see page 7).

There will be a direct screen interface on the application of the robot as well as a direct non-screen interface on the robot. The “power” switch will be both on the robot and on the application and will function as the regular and emergency stop button to cut power to all robot systems. The “power” switch control will be in passive mode: it requires user input to turn on and turn off the power. The application will provide further interaction with the robot as it provides direction buttons that take inputs from users. The robot will also take a series of implicit inputs as default values including the surface mode (flat, incline, or stairs) and the weight of the robot. The direction switch will be in active modes: if the user doesn’t press any direction, the robot will not move.

Several of the indirect interfaces include lights to indicate if the robot is loaded with cargo and to indicate if the robot is in “drive” mode. The constraints of the robot include the restriction on movement if the robot is overweight or if the robot is not in drive mode.

### System Environment

The complexity of stair‐climbing involves more than climbing over an obstacle or going up a slope. For this reason, it is important to take into account the environment in which the system will be operating. The system is expected to operate in a flight of stairs by being able to climb steps one at a time. The location will be Maple Hall in the University of Washington. Each step will have a height of 5⅝ inches, and the stairs will vary in characteristics such as the material and whether or not it is a backed stair. There will also be external entities that may interact with the system such as the weight that the stair climbing robot will be carrying, which will be approximately 1.5 kg.

Since the environment in which the system is expected to operate may vary greatly, this will affect the functionality of the robot. A backless stair means that as the robot moves up the flight of stairs, it can fall through the gap while in the process of moving from one step to another. This means that the robot will have to have a large chassis and large wheels to avoid falling through. Also, the different materials of the stairs may affect the mobility of the robot, with surfaces such as carpeted stairs producing more friction with the wheels. This means the wheel design has to be versatile in order to be slicker on rough surfaces and grippy on smooth surfaces.

In terms of external factors to the stairs, people walking up or down the stairs can impede the robot’s movement. In addition, if the robot were to drive outdoors, precipitation or wind can also cause problems for the robot’s stair traversal. Currently the robot is only intended to be driven indoors, but an outdoor modification for the robot would include shielding for the electronics and sensors to detect for people.

### System Input/Output

Figure 2 details how the robot will process different bluetooth commands it will be given. The commands will be a variety of driving instructions that can cause the robot to go in four different direction; forward, backward, to the left and forward, and to the right and forward. The Arduino on board of the robot will interpret each command and power the motors in the commanded way.

The direct processes occurring on the Arduino will be certain motor operations given to each of the independently powered wheels. This will include instructions for the number of rotations each motor needs to make (given in units of seconds) and a direction (a boolean value for forward if true and backwards for false). In the case of all wheels given a time and positive boolean, the robot will drive forward. In the same case but a negative boolean, the robot will drive backward. In the case only the right wheels are told to drive, the robot will turn right. In the case only the left wheels are told to drive, the robot will turn left.

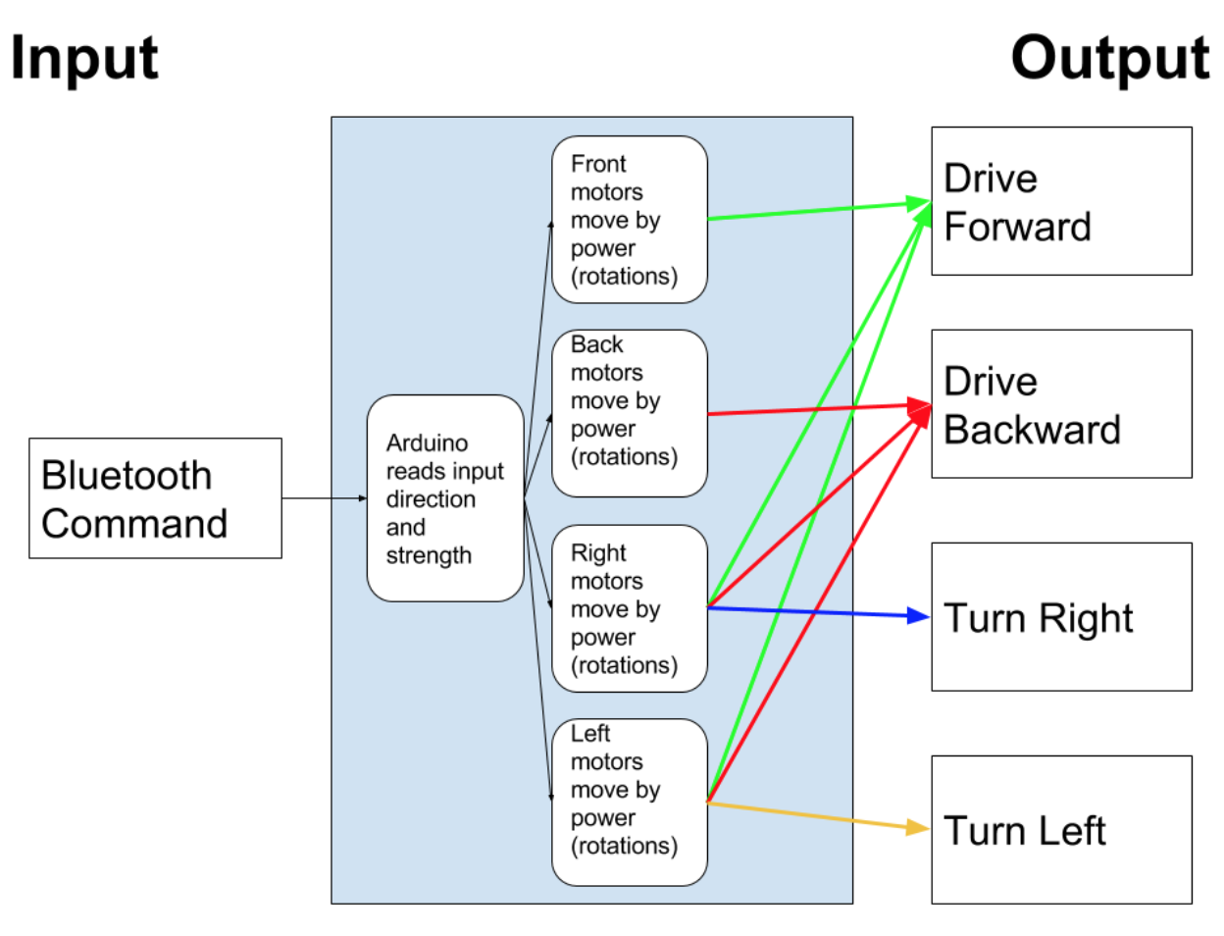
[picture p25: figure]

Figure 2: I/O Diagram

### Concept Sketches

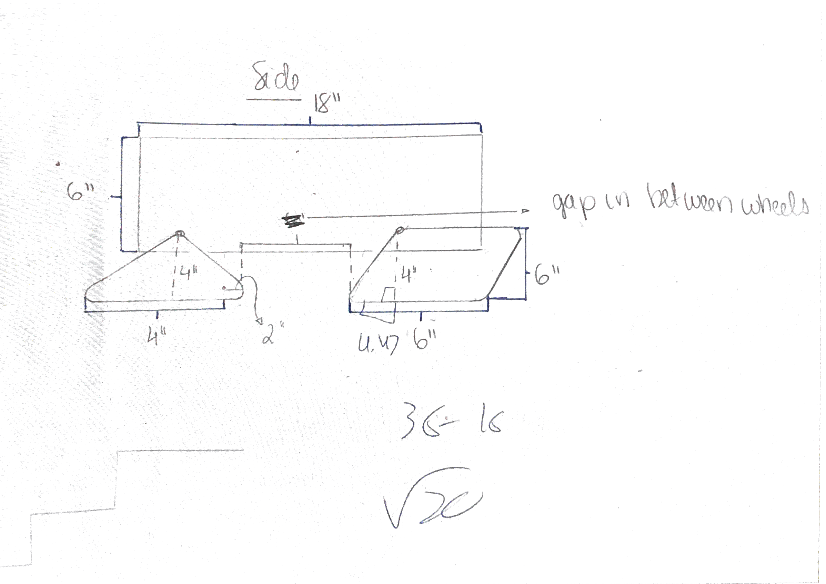
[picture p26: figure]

Figure 3: Concept Sketches - 1

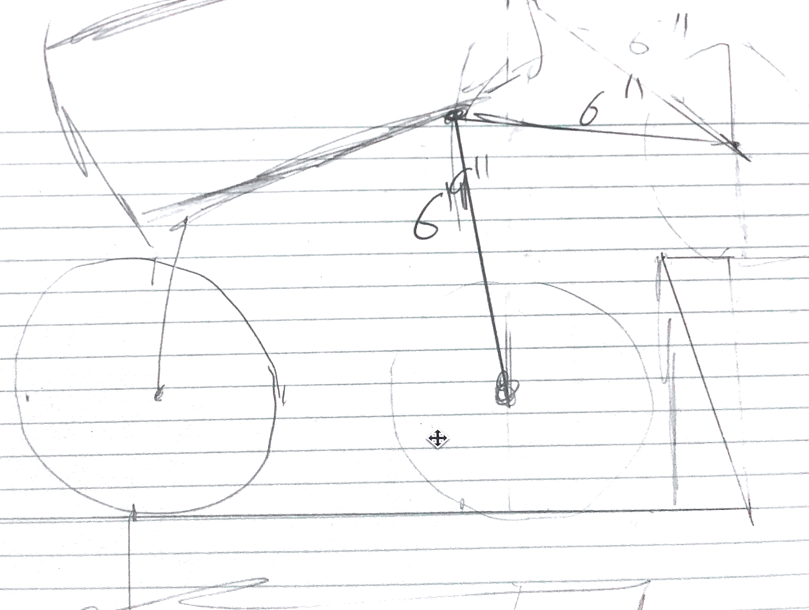
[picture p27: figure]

Figure 4: Concept Sketches – 2

### Preliminary Technical Drawing

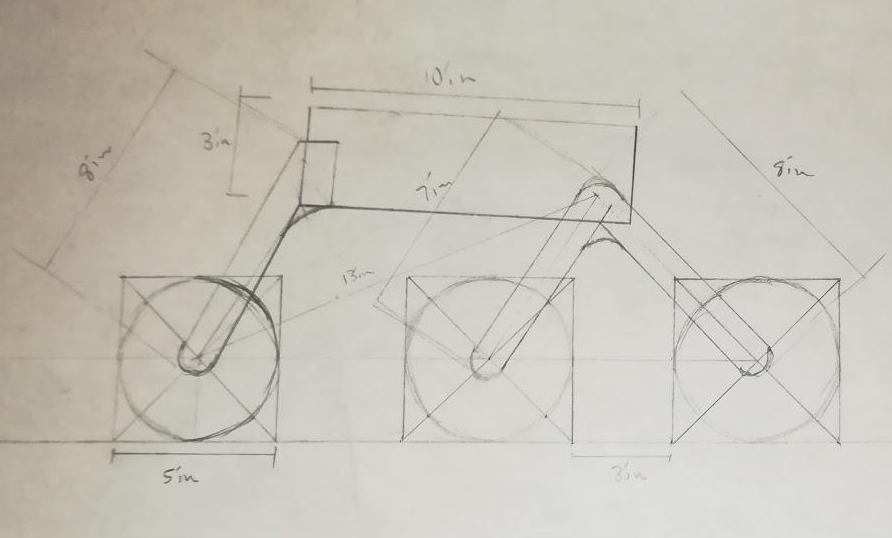
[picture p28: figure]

Figure 5: Preliminary Technical Drawing – 1

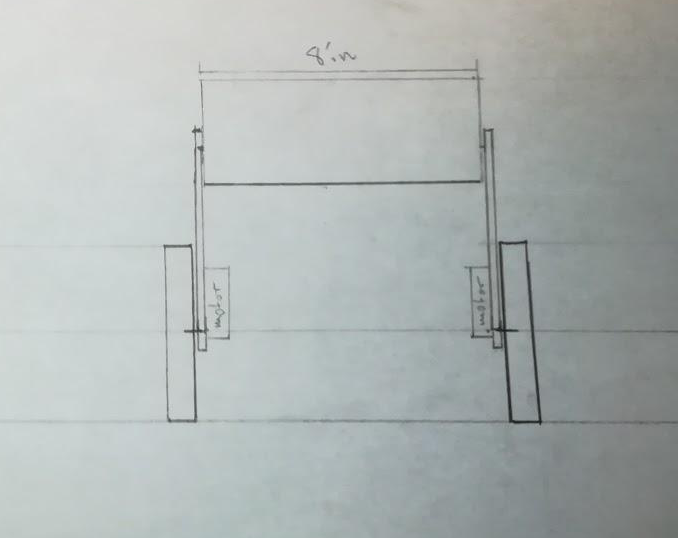
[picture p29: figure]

Figure 6: Preliminary Technical Drawing – 2

The robot will have a 6-wheel design with the forward two front wheels attached together to better climb stairs and the back wheel providing stable support. Each wheel will be of the same composition and size. The brackets that attach the chassis to the wheels will also include springs (Technical Drawing 1) which will allow controlled movement of the wheels. Each wheel will also have attached motors on the underside of the robot (Technical Drawing 2). The chassis is meant to be small and lightweight in order to store the battery, Arduino, Bluetooth module, and additional weight in a safe and enclosed manner.

### Updated Bill of Materials

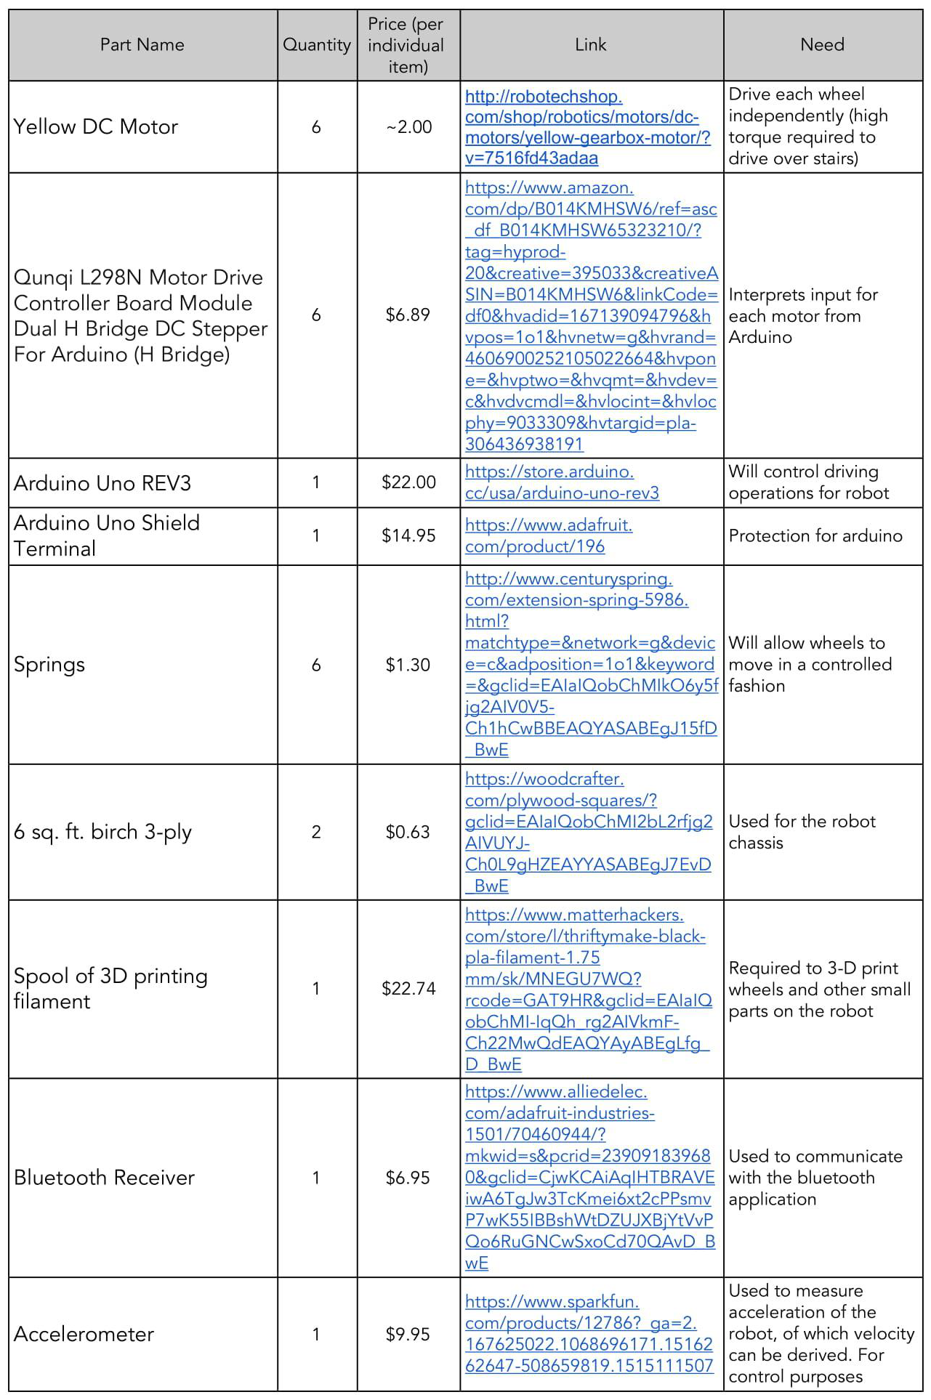
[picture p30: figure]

Table 1: Updated Bill of Materials Table

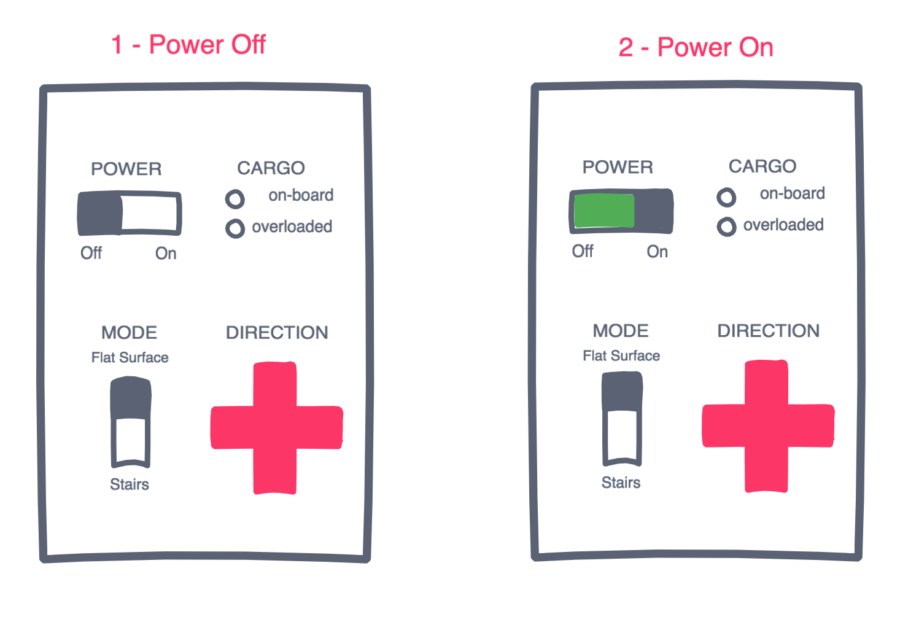
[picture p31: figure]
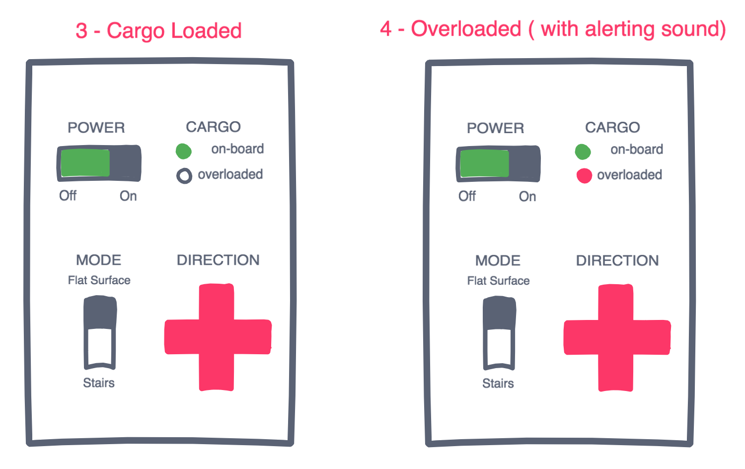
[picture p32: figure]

(see back)


ENGR202 – Winter 2018 Team 9

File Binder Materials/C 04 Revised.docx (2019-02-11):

Aaron Su

Caelen Coe

Noah Whelan

Mahamed Dirie

Rhea Chen

Valentina Valero

# Design Concept

### Design Requirements

The project will be a bluetooth-driven, stair-climbing robot. The robot will be capable of climbing stairs of which each step is 5 inches tall and 12 inches long through a multi-wheeled design. The robot will also have to pull up a 1.5-kilogram weight, making the design of the robot light and sturdy but also requiring independently driven wheels. Finally, the robot will have to have its own power source and Arduino in order to be controlled over bluetooth.

User Interface

The main users of the project will be staffs or drivers who will control the robot to travel to a desired destination, either with or without cargos. Our users are intended to have similar skill and ability as actual users of a commercial stair-climbing robot, such as security officials, military officers, or professional movers. Considering our users’ diverse cognitive affordances, such as language, and education background, we will implement our user interface on either a tablet or on a remote controller, with buttons labeled with universal symbols and colored in shared convention (Figure 1, see page 7).

There will be a direct screen interface on the application of the robot as well as a direct non-screen interface on the robot. The “power” switch will be both on the robot and on the application and will function as the regular and emergency stop button to cut power to all robot systems. The “power” switch control will be in passive mode: it requires user input to turn on and turn off the power. The application will provide further interaction with the robot as it provides direction buttons that take inputs from users. The robot will also take a series of implicit inputs as default values including the surface mode (flat, incline, or stairs) and the weight of the robot. The direction switch will be in active modes: if the user doesn’t press any direction, the robot will not move.

Several of the indirect interfaces include lights to indicate if the robot is loaded with cargo and to indicate if the robot is in “drive” mode. The constraints of the robot include the restriction on movement if the robot is overweight or if the robot is not in drive mode.

### System Environment

The complexity of stair‐climbing involves more than climbing over an obstacle or going up a slope. For this reason, it is important to take into account the environment in which the system will be operating. The system is expected to operate in a flight of stairs by being able to climb steps one at a time. The location will be Maple Hall in the University of Washington. Each step will have a height of 5⅝ inches, and the stairs will vary in characteristics such as the material and whether or not it is a backed stair. There will also be external entities that may interact with the system such as the weight that the stair climbing robot will be carrying, which will be approximately 1.5 kg.

Since the environment in which the system is expected to operate may vary greatly, this will affect the functionality of the robot. A backless stair means that as the robot moves up the flight of stairs, it can fall through the gap while in the process of moving from one step to another. This means that the robot will have to have a large chassis and large wheels to avoid falling through. Also, the different materials of the stairs may affect the mobility of the robot, with surfaces such as carpeted stairs producing more friction with the wheels. This means the wheel design has to be versatile in order to be slicker on rough surfaces and grippy on smooth surfaces.

In terms of external factors to the stairs, people walking up or down the stairs can impede the robot’s movement. In addition, if the robot were to drive outdoors, precipitation or wind can also cause problems for the robot’s stair traversal. Currently the robot is only intended to be driven indoors, but an outdoor modification for the robot would include shielding for the electronics and sensors to detect for people.

### System Input/Output

Figure 2 details how the robot will process different bluetooth commands it will be given. The commands will be a variety of driving instructions that can cause the robot to go in four different direction; forward, backward, to the left and forward, and to the right and forward. The Arduino on board of the robot will interpret each command and power the motors in the commanded way.

The direct processes occurring on the Arduino will be certain motor operations given to each of the independently powered wheels. This will include instructions for the number of rotations each motor needs to make (given in units of seconds) and a direction (a boolean value for forward if true and backwards for false). In the case of all wheels given a time and positive boolean, the robot will drive forward. In the same case but a negative boolean, the robot will drive backward. In the case only the right wheels are told to drive, the robot will turn right. In the case only the left wheels are told to drive, the robot will turn left.

Figure 2: I/O Diagram


### Concept Sketches


Figure 3: Concept Sketches - 1


Figure 4: Concept Sketches – 2

### Preliminary Technical Drawing


Figure 5: Preliminary Technical Drawing – 1(Side View)


Figure 6: Preliminary Technical Drawing – 2 (Front View)

The first design (Figure 5 and 6) will have a 6-wheel design with the forward two front wheels attached together to better climb stairs and the back wheel providing stable support (Figure 5). Each wheel will be of the same composition and size. The brackets that attach the chassis to the wheels will also include springs (Figure 5) which will allow controlled movement of the wheels. Each wheel will also have attached motors on the underside of the robot (Figure 6). The chassis is meant to be small and lightweight in order to store the battery, Arduino, Bluetooth module, and additional weight in a safe and enclosed manner.


Figure 7: Design 2, Small Sprocket Technical Drawing


Figure 8: Design 2, Track Technical Drawing


Figure 9: Design 2, Track Technical Drawing


Figure 10: Design 2, Isometric View of Parts

The second design (Figure 7, 8, 9, and 10) shows a full track in place of wheels that will provide the main support to climb over stairs. The tracks (Figures 8 and 9) will be attached to the the chassis and be powered with gears (Figure 7). The final form of the robot of Design 2 (Figure 10) shows that the wheel design, which might fail on stairs without a backing, can be overcome with this particular arrangement of parts. Both designs will be prototyped going forward. The tracks will be powered with 4 motors, one on each corner of the vehicle.

### Updated Bill of Materials


Table 1: Updated Bill of Materials Table


(see back)


ENGR202 – Winter 2018 Team 9

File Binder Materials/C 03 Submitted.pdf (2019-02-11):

ENGR202 – Winter 2018 | Team 9 | 1

Aaron Su
Caelen Coe
Noah Whelan
Mahamed Dirie
Rhea Chen
Valentina Valero

Design Concept

Design Requirements
The project will be a bluetooth-driven, stair-climbing robot. The robot will be capable of climbing stairs of which each step is 5 inches tall and 12 inches long through a multi-wheeled design. The robot will also have to pull up a 1.5-kilogram weight, making the design of the robot light and sturdy but also requiring independently driven wheels. Finally, the robot will have to have its own power source and Arduino in order to be controlled over bluetooth.

User Interface
The main users of the project will be staffs or drivers who will control the robot to travel to a desired destination, either with or without cargos. Our users are intended to have similar skill and ability as actual users of a commercial stair-climbing robot, such as security officials, military officers, or professional movers. Considering our users’ diverse cognitive affordances, such as language, and education background, we will implement our user interface on either a tablet or on a remote controller, with buttons labeled with universal symbols and colored in shared convention (Figure 1, see page 7).

There will be a direct screen interface on the application of the robot as well as a direct non-screen interface on the robot. The “power” switch will be both on the robot and on the application and will function as the regular and emergency stop button to cut power to all robot systems. The “power” switch control will be in passive mode: it requires user input to turn on and turn off the power. The application will provide further interaction with the robot as it provides direction buttons that take inputs from users. The robot will also take a series of implicit inputs as default values including the surface mode (flat, incline, or stairs) and the weight of the robot. The direction switch will be in active modes: if the user doesn’t press any direction, the robot will not move.

Several of the indirect interfaces include lights to indicate if the robot is loaded with cargo and to indicate if the robot is in “drive” mode. The constraints of the robot include the restriction on movement if the robot is overweight or if the robot is not in drive mode.

System Environment
The complexity of stair‐climbing involves more than climbing over an obstacle or going up a slope. For this reason, it is important to take into account the environment in which the system will be operating. The system is expected to operate in a flight of stairs by being able to climb steps one at a time. The location will be Maple Hall in the University of Washington. Each step will have a height of 5⅝ inches, and the stairs will vary in characteristics such as the material and whether or not it is a backed stair. There will also be external entities that may interact with the system such as the weight that the stair climbing robot will be carrying, which will be approximately 1.5 kg.

Since the environment in which the system is expected to operate may vary greatly, this will affect the functionality of the robot. A backless stair means that as the robot moves up the flight of stairs, it can fall through the gap while in the process of moving from one step to another. This means that the robot will have to have a large chassis and large wheels to avoid falling through. Also, the different materials of the stairs may affect the mobility of the robot, with surfaces such as carpeted stairs producing more friction with the wheels. This means the wheel design has to be versatile in order to be slicker on rough surfaces and grippy on smooth surfaces.

In terms of external factors to the stairs, people walking up or down the stairs can impede the robot’s movement. In addition, if the robot were to drive outdoors, precipitation or wind can also cause problems for the robot’s stair traversal. Currently the robot is only intended to be driven indoors, but an outdoor modification for the robot would include shielding for the electronics and sensors to detect for people.

System Input/Output
Figure 2 details how the robot will process different bluetooth commands it will be given. The commands will be a variety of driving instructions that can cause the robot to go in four different direction; forward, backward, to the left and forward, and to the right and forward. The Arduino on board of the robot will interpret each command and power the motors in the commanded way.

The direct processes occurring on the Arduino will be certain motor operations given to each of the independently powered wheels. This will include instructions for the number of rotations each motor needs to make (given in units of seconds) and a direction (a boolean value for forward if true and backwards for false). In the case of all wheels given a time and positive boolean, the robot will drive forward. In the same case but a negative boolean, the robot will drive backward. In the case only the right wheels are told to drive, the robot will turn right. In the case only the left wheels are told to drive, the robot will turn left.


Figure 2: I/O Diagram


Concept Sketches

Figure 3: Concept Sketches - 1

Figure 4: Concept Sketches – 2

Preliminary Technical Drawing


Figure 5: Preliminary Technical Drawing – 1


Figure 6: Preliminary Technical Drawing – 2

The robot will have a 6-wheel design with the forward two front wheels attached together to better climb stairs and the back wheel providing stable support. Each wheel will be of the same composition and size. The brackets that attach the chassis to the wheels will also include springs (Technical Drawing 1) which will allow controlled movement of the wheels. Each wheel will also have attached motors on the underside of the robot (Technical Drawing 2). The chassis is meant to be small and lightweight in order to store the battery, Arduino, Bluetooth module, and additional weight in a safe and enclosed manner.

Updated Bill of Materials


Table 1: Updated Bill of Materials Table


(see back)


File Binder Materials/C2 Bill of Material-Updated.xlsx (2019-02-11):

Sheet: updated
Part Name | Quantity | Price (per individual item) | Link | Need
Yellow DC Motor | 6 | ~2.00 | http://robotechshop.com/shop/robotics/motors/dc-motors/yellow-gearbox-motor/?v=7516fd43adaa | Drive each wheel independently (high torque required to drive over stairs)
Qunqi L298N Motor Drive Controller Board Module Dual H Bridge DC Stepper For Arduino (H Bridge) | 6 | $6.89 | https://www.amazon.com/dp/B014KMHSW6?creative=395033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 | Interprets input for each motor from Arduino
Arduino Uno REV3 | 1 | $22.00 | https://store.arduino.cc/usa/arduino-uno-rev3 | Will control driving operations for robot
Arduino Uno Shield Terminal | 1 | $14.95 | https://www.adafruit.com/product/196 | Protection for arduino
Springs | 6 | $1.30 | http://www.centuryspring.com/extension-spring-5986.html?matchtype=&network=g&device=c&adposition=1o1&keyword= | Will allow wheels to move in a controlled fashion
6 sq. ft. birch 3-ply | 2 | $0.63 | https://woodcrafter.com/plywood-squares/ | Used for the robot chassis
Spool of 3D printing filament | 1 | $22.74 | https://www.matterhackers.com/store/l/thriftymake-black-pla-filament-1.75mm/sk/MNEGU7WQ?rcode=GAT9HR | Required to 3-D print wheels and other small parts on the robot
Bluetooth Receiver | 1 | $6.95 | https://www.alliedelec.com/adafruit-industries-1501/70460944/?pcrid=239091839680 | Used to communicate with the bluetooth application
Accelerometer | 1 | $9.95 | https://www.sparkfun.com/products/12786?_ga=2.167625022.1068696171.1516262647-508659819.1515111507 | Used to measure acceleration of the robot, of which velocity can be derived. For control purposes

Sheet: Copy of updated
Part Name | Quantity | Price (per individual item) | Link
~~Yellow Gearbox Motors~~ | ~~4~~ | ~~$1.99~~ | ~~http://robotechshop.com/shop/robotics/motors/dc-motors/yellow-gearbox-motor/?v=7516fd43adaa~~
Qunqi L298N Motor Drive Controller Board Module Dual H Bridge DC Stepper For Arduino (H Bridge) | ~~2~~ | $6.89 | https://www.amazon.com/dp/B014KMHSW6?creative=395033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
Arduino Uno REV3 | 1 | $22.00 | https://store.arduino.cc/usa/arduino-uno-rev3
Arduino Uno Shield Terminal | 1 | $14.95 | https://www.adafruit.com/product/196
Springs | ~~4~~ | $1.30 | http://www.centuryspring.com/extension-spring-5986.html?matchtype=&network=g&device=c&adposition=1o1&keyword=
6 sq. ft. birch 3-ply | 2 | $0.63 | https://woodcrafter.com/plywood-squares/
Spool of 3D printing filament | 1 | $22.74 | https://www.matterhackers.com/store/l/thriftymake-black-pla-filament-1.75mm/sk/MNEGU7WQ?rcode=GAT9HR
~~Nylon Bushing~~ | ~~12~~ | ~~$0.24~~ | ~~https://www.mouser.com/ProductDetail/Harwin/R40-6710894/?qs=ulE8k0yEMYbNzsWdS2i7wA%3D%3D
Bluetooth Receiver | 1 | $6.95 | https://www.alliedelec.com/adafruit-industries-1501/70460944/?pcrid=239091839680
Accelerometer | 1 | $9.95 | https://www.sparkfun.com/products/12786?_ga=2.167625022.1068696171.1516262647-508659819.1515111507

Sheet: original
Table 2 - Bill of Materials Table
Part Name | Quantity | Price | Link
Yellow Gearbox Motors | 4 | $1.99 | http://robotechshop.com/shop/robotics/motors/dc-motors/yellow-gearbox-motor/?v=7516fd43adaa
Qunqi L298N Motor Drive Controller Board Module Dual H Bridge DC Stepper For Arduino (H Bridge) | 2 | $6.89 | https://www.amazon.com/dp/B014KMHSW6?creative=395033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
Arduino Uno REV3 | 1 | $22.00 | https://store.arduino.cc/usa/arduino-uno-rev3
Arduino Uno Shield Terminal | 1 | $14.95 | https://www.adafruit.com/product/196
Springs | 4 | $1.30 | http://www.centuryspring.com/extension-spring-5986.html?matchtype=&network=g&device=c&adposition=1o1&keyword=
6 sq. ft. birch 3-ply | 2 | $0.63 | https://woodcrafter.com/plywood-squares/
Spool of 3D printing filament | 1 | $22.74 | https://www.matterhackers.com/store/l/thriftymake-black-pla-filament-1.75mm/sk/MNEGU7WQ?rcode=GAT9HR
Nylon Bushings | 12 | $0.24 | https://www.mouser.com/ProductDetail/Harwin/R40-6710894/?qs=ulE8k0yEMYbNzsWdS2i7wA%3D%3D
Bluetooth Receiver | 1 | $6.95 | https://www.alliedelec.com/adafruit-industries-1501/70460944/?pcrid=239091839680
Accelerometer | 1 | $9.95 | https://www.sparkfun.com/products/12786?_ga=2.167625022.1068696171.1516262647-508659819.1515111507


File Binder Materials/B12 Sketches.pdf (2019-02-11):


auwup” 4:9an

e; 'f_ yrwwu.
Mam“ E333?

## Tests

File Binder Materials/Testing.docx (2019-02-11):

- First trial of all yellow 9V dc motors failed at climbing stairs, but could climb ramp and go down stairs at full speed
- Switch out motors from all yellow to front 12 V 100 rpm and back 12 V 30 rpm to increase torque and power to climb stairs

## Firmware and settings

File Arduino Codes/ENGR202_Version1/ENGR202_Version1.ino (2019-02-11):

// Engineering 202C
// Winter 2018
// Team 9 - Stair Climbing Robot
// University of Washington
// Code written by Aaron Su
// 
// Drives a robot based upon commands given over a bluetooth app. Uses LEDS for user feedback

// Ardunio Pins
const int rx0 = 0; // Bluetooth
const int tx1 = 1; // Bluetooth
const int lT1 = 2; // Direction, Maps to 2 on All HBridges
const int lT2 = 4; // Direction, Maps to 3 on All HBridges
const int lTP = 3; // Power, Maps to 1 on Front Two HBridges
const int rT1 = 5; // Direction, Maps to 5 on All HBridges
const int rT2 = 6; // Direction, Maps to 4 on All HBridges
const int rTP = 7; // Power, Maps to 6 on Front Two Hbridges
const int ledB = 8;
const int ledG = 9;
const int ledR = 10;
const int bLP = 11; // Power, Maps to 1 on Back Hbridge
const int bRP = 12; // Power, Maps to 6 on Back Hbridge
const int unknown = 13; // Does not yet have a purpose

// HBridge Motor Power 
const int FULL_POW = 255;
const int HIGH_POW = 240;
const int MED_POW = 128;
const int LOW_POW = 32;

// LED Constants
const int BRIGHT = 250;
const int DIM = 64;
const int OFF = 0;

char incomingByte; // Global variable for BT input

// Main drive program that will control the robot's movements
void drive() 
{
   if(Serial.available() > 0) // Bluetooth connected
  {
    resetColors();
    analogWrite(ledB, 255);
    incomingByte = Serial.read();
    if(incomingByte == 'f') {
      // Color
      resetColors();
      analogWrite(ledG, 255);
      
      // Drive
      analogWrite(lTP, FULL_POW);
      analogWrite(rTP, FULL_POW);
      analogWrite(bLP, HIGH_POW);
      analogWrite(bRP, HIGH_POW);
      digitalWrite(lT1, LOW);
      digitalWrite(lT2, HIGH);
      digitalWrite(rT1, LOW);
      digitalWrite(rT2, HIGH);
      
      // Send message
      Serial.print("Forward");
    } 
    else if (incomingByte == 'b') 
    {
      // Color
      resetColors();
      analogWrite(ledG, 255);
      analogWrite(ledR, 255);
      
      // Drive
      analogWrite(ledG, 255);
      analogWrite(ledB, 0);
      analogWrite(lTP, 255);
      analogWrite(rTP, 255);
      analogWrite(bLP, 255);
      analogWrite(bRP, 255);
      digitalWrite(lT1, HIGH);
      digitalWrite(lT2, LOW);
      digitalWrite(rT1, HIGH);
      digitalWrite(rT2, LOW);
      
      // Send message
      Serial.print("Backward");
    }
  } 
  else // Bluetooth not connected
  {
    // Color
    resetColors();
    analogWrite(ledR, 255);
  }
  
}

void resetColors() 
{
  analogWrite(ledR, 0);
  analogWrite(ledG, 0);
  analogWrite(ledB, 0);

}

// Demo to test Motors
void demoOne()
{
  // this function will run the motors in both directions at a fixed speed
  // turn on motor A
  digitalWrite(lT1, HIGH);
  digitalWrite(lT2, LOW);
  // set speed to 200 out of possible range 0~255
  analogWrite(lTP, 200);
  // now change motor directions
  digitalWrite(lT1, LOW);
  digitalWrite(lT2, HIGH);  
  delay(2000);
  // now turn off motors
  digitalWrite(lT1, LOW);
  digitalWrite(lT2, LOW);  
}

// Autonomous testing program
void demoTwo() {
  
}

// Checkpoint demo to show functionality of all parts
void checkPointDemo() {
  // Send a bluetooth message
  // Recieve a bluetooth message
  // Turn on LED to 3 different colors
  // Drive all motors forward
  // Drive all motors backwards
}

void setup() 
{
    Serial.begin(9600); // Open BT connection
    //pinMode(rx0, OUTPUT); 
    //pinMode(tx1, OUTPUT);
    pinMode(lT1, OUTPUT);
    pinMode(lT2, OUTPUT);
    digitalWrite(lTP, LOW);
    pinMode(rT1, OUTPUT);
    pinMode(rT2, OUTPUT);
    digitalWrite(rTP, LOW);
    pinMode(ledR, OUTPUT);
    pinMode(ledG, OUTPUT);
    pinMode(ledB, OUTPUT);
    digitalWrite(bLP, LOW);
    digitalWrite(bRP, LOW);
    analogWrite(ledR, 255);
}

void loop() 
{
  demoOne();
  delay(1000);
}
